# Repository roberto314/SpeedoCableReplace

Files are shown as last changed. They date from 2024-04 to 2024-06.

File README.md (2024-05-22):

# SpeedoCableReplace
An electronic replacement for a Speedometer Cable from an old car.

This is a simple solution for a broken speedometer cable. 
It uses a sensor on the wheels or on the propshaft and converts
it to a PWM for a small BLDC Motor.
I found some on ebay. They look like this:

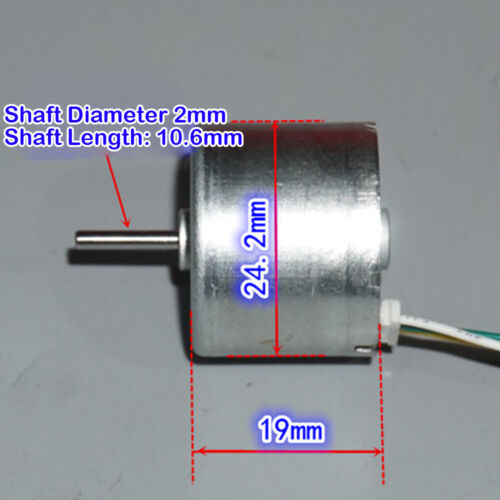
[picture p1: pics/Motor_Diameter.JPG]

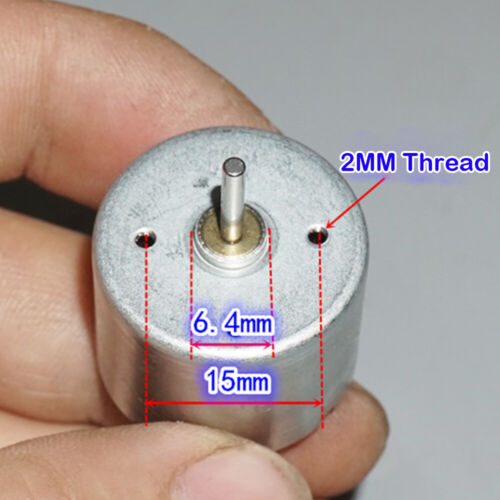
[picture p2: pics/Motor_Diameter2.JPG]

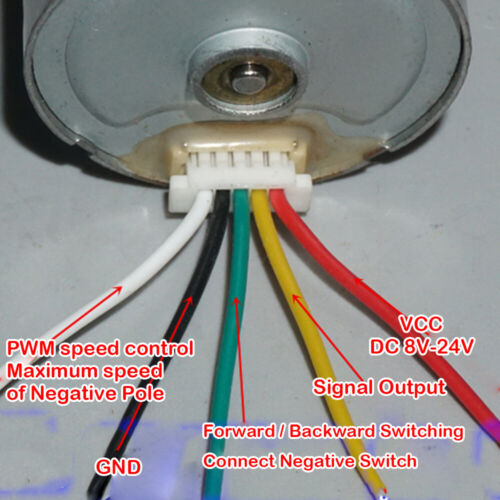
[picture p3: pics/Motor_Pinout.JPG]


This motor should be mounted to the speedometer. The microcontroller is a STM32F103 
maple mini board. The firmware is based on ChibiOS 20 (trunk).

Schematic:

[Schematic](schematics/pdf/Tachoconverter.pdf)

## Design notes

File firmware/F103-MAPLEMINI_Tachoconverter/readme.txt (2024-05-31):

*****************************************************************************
** ChibiOS/RT port for ARM-Cortex-M3 STM32F103 on LeafLabs MapleMini       **
*****************************************************************************

** TARGET **

Tachoconverter

The demo runs on the MapleMini without the original MapleMini bootloader.
Serial Shell @ 38400 Baud, External I2C EPROM, PWM and ICP.

Pinout:
GPIO - mbed - Voltage
PA0  - 11  - 3V3 - free PWM2/1
PA1  - 10  - 3V3 - /HC05ON
PA2  -  9  - 3V3 - TX2 (Console + Debug)
PA3  -  8  - 3V3 - RX2 (Console + Debug)
PA4  -  7  - 3V3 - free
PA5  -  6  - 3V3 - free SPI1 SCK
PA6  -  5  - 3V3 - free SPI1 MISO
PA7  -  4  - 3V3 - free SPI1 MOSI
PA8  - 27  -  5V - VehicleSpeed In PWM1/1
PA9  - 26  -  5V - free PWM1/2
PA10 - 25  -  5V - free PWM1/3
PA11 - 24  -  5V - USD DM 
PA12 - 23  -  5V - USB DP 
PA13 - 22  -  5V - SWDIO
PA14 - 21  -  5V - SWCLK
PA15 - 20  -  5V - free PWM2/1
PB0  -  3  - 3V3 - free
PB1  -  -  -  5V - LED
PB2  -  2  -  5V - free boot
PB3  - 19  -  5V - MotorSpeed In PWM2/2 remap
PB4  - 18  -  5V - CW/CCW PWM3/1
PB5  - 17  - 3V3 - free PWM3/2
PB6  - 16  -  5V - SCL (EPROM)
PB7  - 15  -  5V - SDA (EPROM)
PB8  - but -  5V - MotorPWM Out PWM4/3
PB9  -  -  -  5V - USB_CON
PB10 -  1  -  5V - free PWM2/3
PB11 -  0  -  5V - free PWM2/4
PB12 -  31 -  5V - HC05 State
PB13 -  30 -  5V - free PWM1/1N
PB14 -  29 -  5V - free PWM1/2N
PB15 -  28 -  5V - free PWM1/3N
PC13 -  14 - 3V3 - EPROM WP
PC14 -  13 - 3V3 - HC05 Enable
PC15 -  12 - 3V3 - free

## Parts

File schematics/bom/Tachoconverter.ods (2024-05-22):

Designator | Footprint | Quantity | Designation | Supplier and ref
U2 | TO-220-3_Vertical | 1 | L7805
JP1 | PinHeader_1x03_P2.54mm_Vertical | 1 | SensorVcc
J3 | TerminalBlock_MetzConnect_Type094_RT03505HBLU_1x05_P5.00mm_Horizontal | 1 | Input
A1 | Maple_Mini | 1 | Maple_Mini
J1 | TerminalBlock_MetzConnect_Type094_RT03505HBLU_1x05_P5.00mm_Horizontal | 1 | Motor
D1 | D_SMA | 1 | 1N4007
R5,R6,R1 | R_1206_3216Metric_Pad1.30x1.75mm_HandSolder | 3 | 1k
C3,C1 | CP_EIA-7343-31_Kemet-D | 2 | 100u/25
U1 | DIP-8_W7.62mm_Socket_LongPads | 1 | AT24CS64-SSHM
R2,R4,R3 | R_1206_3216Metric_Pad1.30x1.75mm_HandSolder | 3 | 10k
D2 | SOT-23_Handsoldering | 1 | BAV99
C4,C2 | C_1206_3216Metric_Pad1.33x1.80mm_HandSolder | 2 | 100n
U5 | SOIC-14_3.9x8.7mm_P1.27mm | 1 | 74HC14

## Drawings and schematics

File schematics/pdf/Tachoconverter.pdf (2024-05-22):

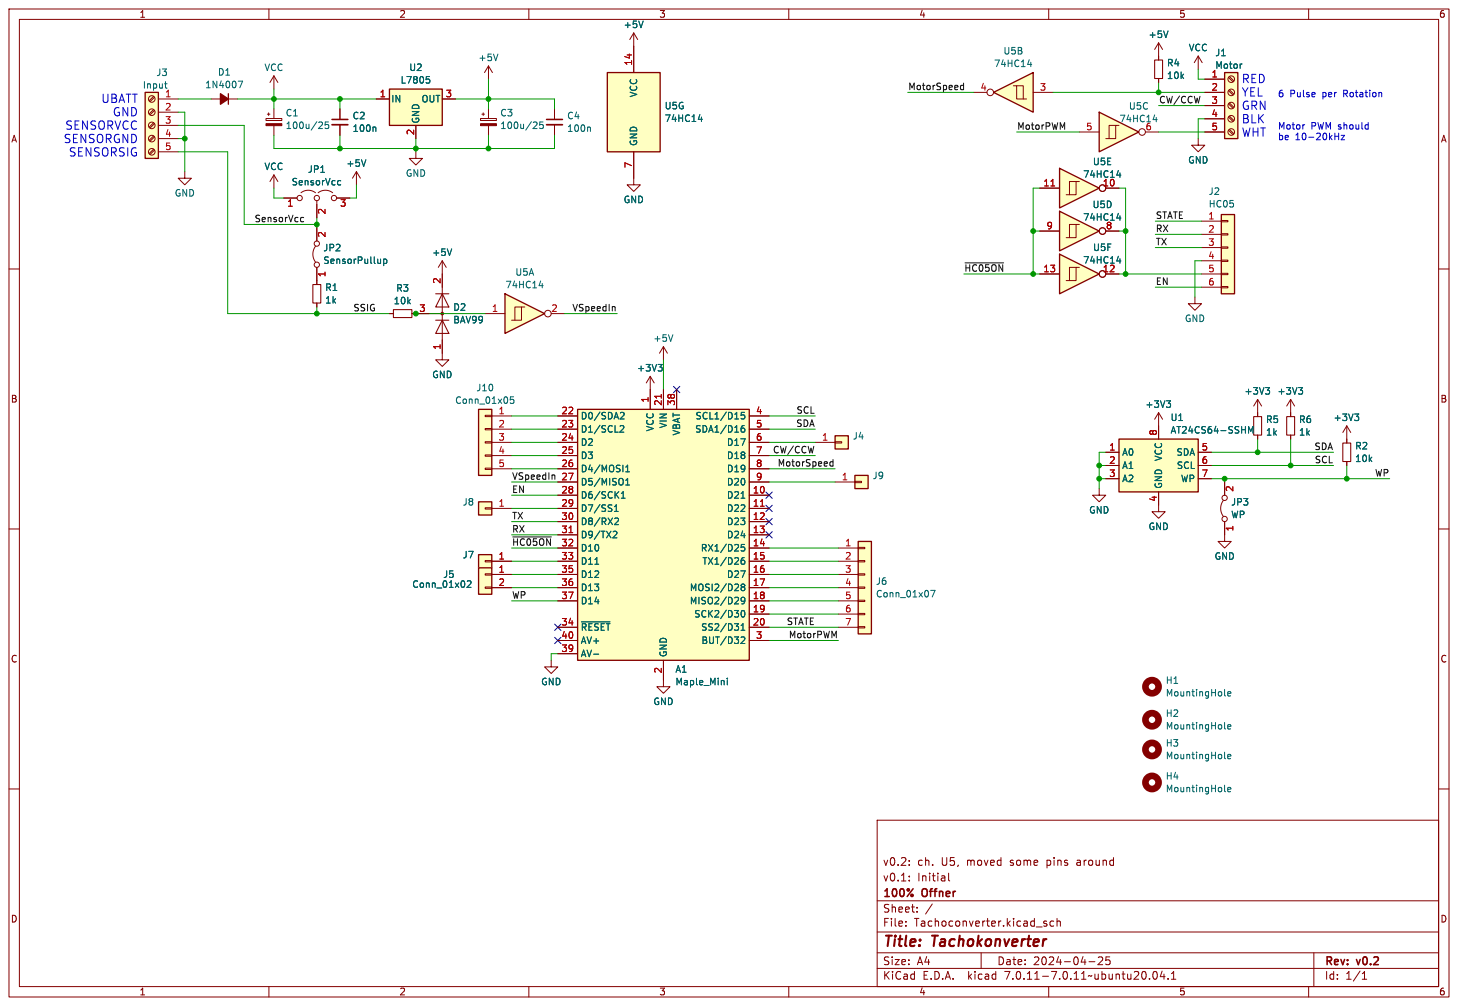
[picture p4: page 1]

6 Pulse per Rotation Motor PWM should

A1Maple_Mini VCC
SDA MotorSpeed STATE MotorPWM

H1 MountingHole H2 MountingHole H3 MountingHole H4 MountingHole GND

2 SS2/D31 20 VIN 21 D0/SDA2 22 D1/SCL2 23 D2 24 D3 25 D4/MOSI1 26 D5/MISO1 27 D6/SCK1 28 D7/SS1 29 BUT/D32 3 D8/RX2 30 D9/TX2 31 D10 32 D11 33 ~{RESET} 34 D12 35 D13 36 D14 37 VBAT 38 AV- 39 SCL1/D15 4 AV+ 40 SDA1/D16 5 D17 6 D18 7 D19 8 D20 9 GND GND

2 SS2/D31 20 VIN 21 D0/SDA2 22 D1/SCL2 23 D2 24 D3 25 D4/MOSI1 26 D5/MISO1 27 D6/SCK1 28 D7/SS1 29 BUT/D32 3 D8/RX2 30 D9/TX2 31 D10 32 D11 33 ~{RESET} 34 D12 35 D13 36 D14 37 VBAT 38 AV- 39 SCL1/D15 4 AV+ 40 SDA1/D16 5 D17 6 D18 7 D19 8 D20 9 A1Maple_Mini GND

4 SDA 5 SCL 6 WP 7 VCC
JP3 WP GND

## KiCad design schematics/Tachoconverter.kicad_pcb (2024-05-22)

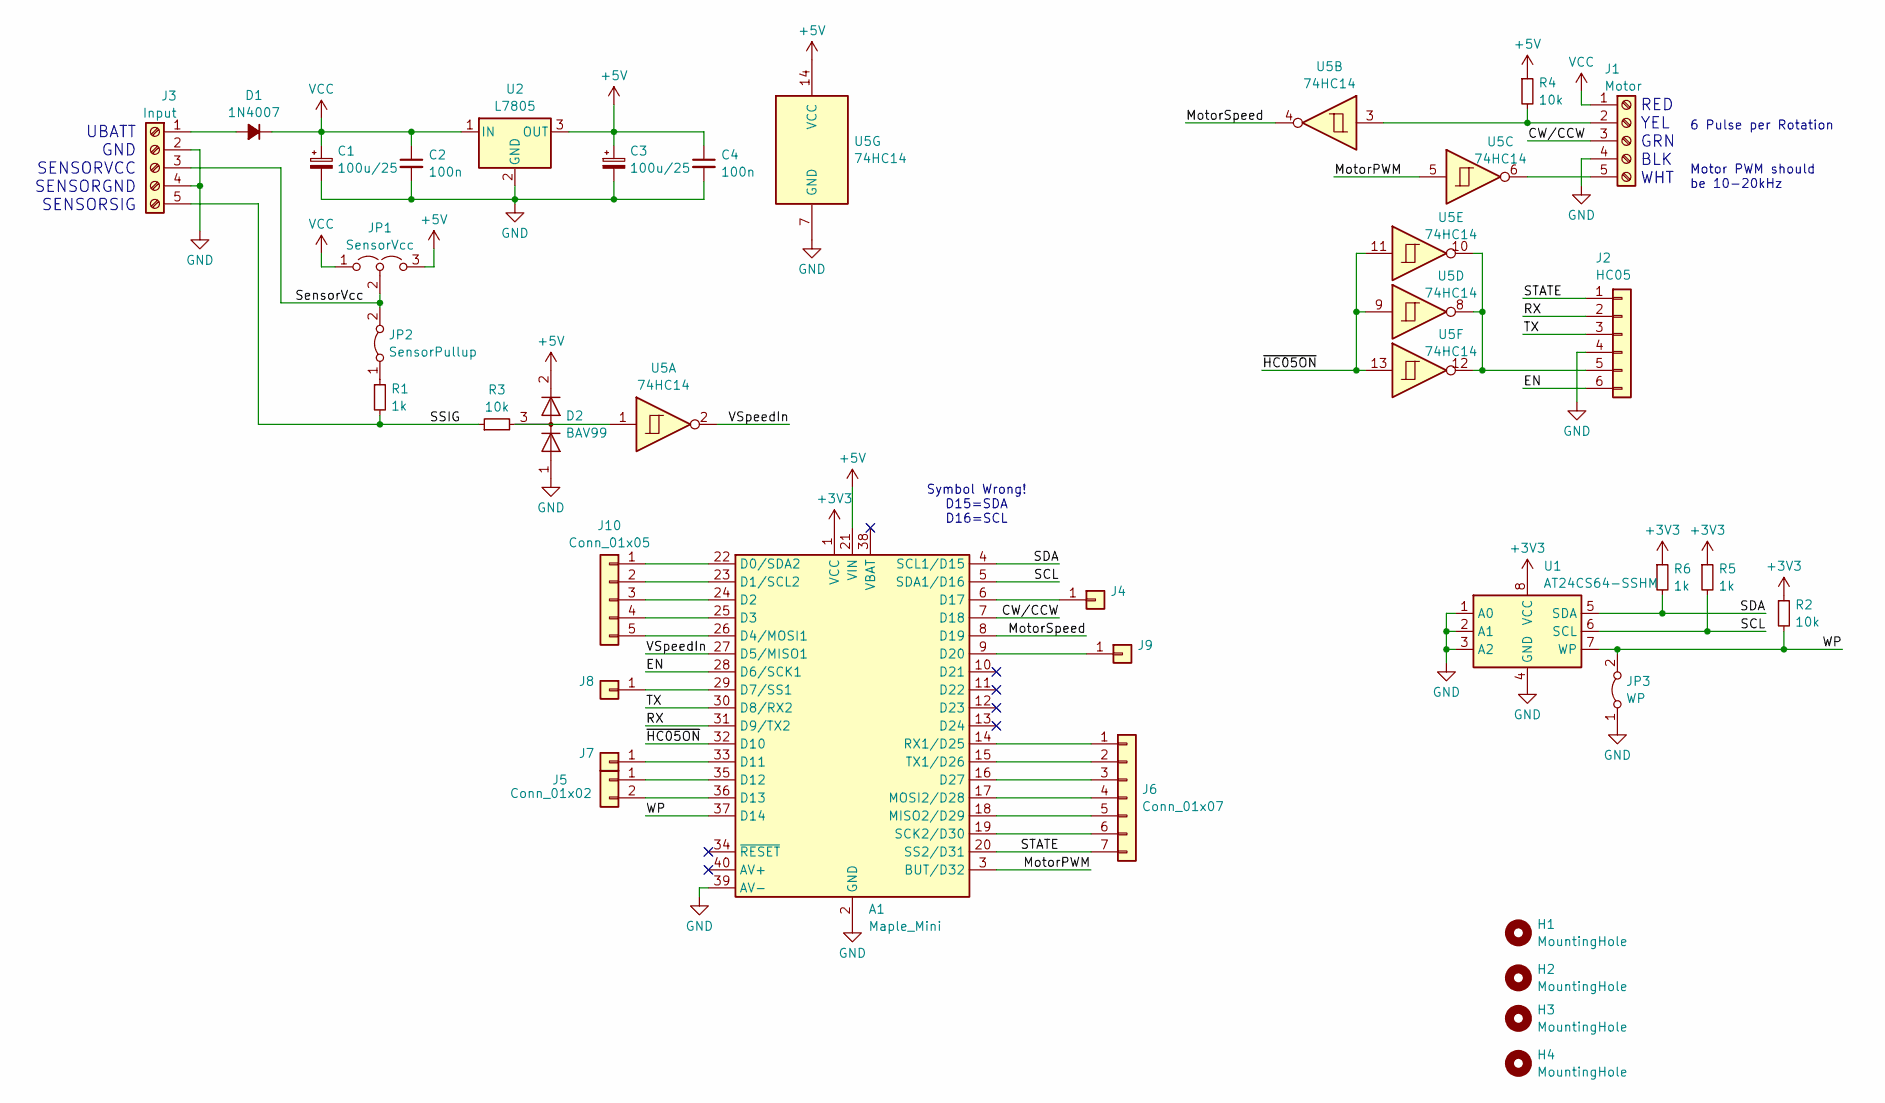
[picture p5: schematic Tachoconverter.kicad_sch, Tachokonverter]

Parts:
A1: Maple_Mini
C1, C3: 100u/25; CP_EIA-7343-31_Kemet-D
C2, C4: 100n; C_1206_3216Metric_Pad1.33x1.80mm_HandSolder
D1: 1N4007; D_SMA
D2: BAV99; SOT-23_Handsoldering
H1, H2, H3, H4: MountingHole; MountingHole_3.2mm_M3
J1: Motor; TerminalBlock_MetzConnect_Type094_RT03505HBLU_1x05_P5.00mm_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
J2: HC05; PinHeader_1x06_P2.54mm_Vertical
J3: Input; TerminalBlock_MetzConnect_Type094_RT03505HBLU_1x05_P5.00mm_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
J4, J7, J8, J9: Conn_01x01; PinHeader_1x01_P2.54mm_Vertical
J5: Conn_01x02; PinHeader_1x02_P2.54mm_Vertical
J6: Conn_01x07; PinHeader_1x07_P2.54mm_Vertical
J10: Conn_01x05; PinHeader_1x05_P2.54mm_Vertical
JP1: SensorVcc; PinHeader_1x03_P2.54mm_Vertical
JP2: SensorPullup; SolderJumper-2_P1.3mm_Bridged_RoundedPad1.0x1.5mm
JP3: WP; SolderJumper-2_P1.3mm_Bridged_RoundedPad1.0x1.5mm
R1, R5, R6: 1k; R_1206_3216Metric_Pad1.30x1.75mm_HandSolder
R2, R3, R4: 10k; R_1206_3216Metric_Pad1.30x1.75mm_HandSolder
U1: AT24CS64-SSHM; DIP-8_W7.62mm_Socket_LongPads
U2: L7805; TO-220-3_Vertical
U5: 74HC14; SOIC-14_3.9x8.7mm_P1.27mm

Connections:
+3V3: A1.1 (VCC), R2.1, R5.1, R6.1, U1.8 (VCC)
+5V: A1.21 (VIN), C3.1, C4.1, D2.2 (A), JP1.3 (B), R4.1, U2.3 (OUT), U5.14 (VCC)
/CW/CCW: A1.7 (D18), J1.3
/EN: A1.28 (D6/SCK1), J2.6
/MotorPWM: A1.3 (BUT/D32), U5.5
/MotorSpeed: A1.8 (D19), U5.4
/RX: A1.31 (D9/TX2), J2.2
/SCL: A1.5 (SDA1/D16), R5.2, U1.6 (SCL)
/SDA: A1.4 (SCL1/D15), R6.2, U1.5 (SDA)
/SSIG: J3.5, R1.2, R3.1
/STATE: A1.20 (SS2/D31), J2.1, J6.7
/SensorVcc: J3.3, JP1.2 (C), JP2.2 (B)
/TX: A1.30 (D8/RX2), J2.3
/VSpeedIn: A1.27 (D5/MISO1), U5.2
/WP: A1.37 (D14), JP3.2 (B), R2.2, U1.7 (WP)
/~HC05ON: A1.32 (D10), U5.9, U5.11, U5.13
GND: A1.2 (GND), A1.39 (AV-), C1.2, C2.2, C3.2, C4.2, D2.1 (K), J1.4, J2.4, J3.2, J3.4, JP3.1 (A), U1.1 (A0), U1.2 (A1), U1.3 (A2), U1.4 (GND), U2.2 (GND), U5.7 (GND)
unnamed: A1.22 (D0/SDA2), J10.1
unnamed: A1.23 (D1/SCL2), J10.2
unnamed: A1.24 (D2), J10.3
unnamed: A1.25 (D3), J10.4
unnamed: A1.26 (D4/MOSI1), J10.5
unnamed: A1.29 (D7/SS1), J8.1
unnamed: A1.33 (D11), J7.1
unnamed: A1.35 (D12), J5.1
unnamed: A1.36 (D13), J5.2
unnamed: A1.6 (D17), J4.1
unnamed: A1.9 (D20), J9.1
unnamed: A1.16 (D27), J6.3
unnamed: A1.18 (MISO2/D29), J6.5
unnamed: A1.17 (MOSI2/D28), J6.4
unnamed: A1.14 (RX1/D25), J6.1
unnamed: A1.19 (SCK2/D30), J6.6
unnamed: A1.15 (TX1/D26), J6.2
unnamed: D1.2 (A), J3.1
unnamed: D2.3 (K), R3.2, U5.1
unnamed: J1.2, R4.2, U5.3
unnamed: J1.5, U5.6
unnamed: J2.5, U5.8, U5.10, U5.12
unnamed: JP2.1 (A), R1.1
VCC: C1.1, C2.1, D1.1 (K), J1.1, JP1.1 (A), U2.1 (IN)

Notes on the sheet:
Symbol Wrong! D15=SDA D16=SCL
RED YEL GRN BLK WHT
6 Pulse per Rotation
Motor PWM should be 10-20kHz
UBATT GND SENSORVCC SENSORGND SENSORSIG

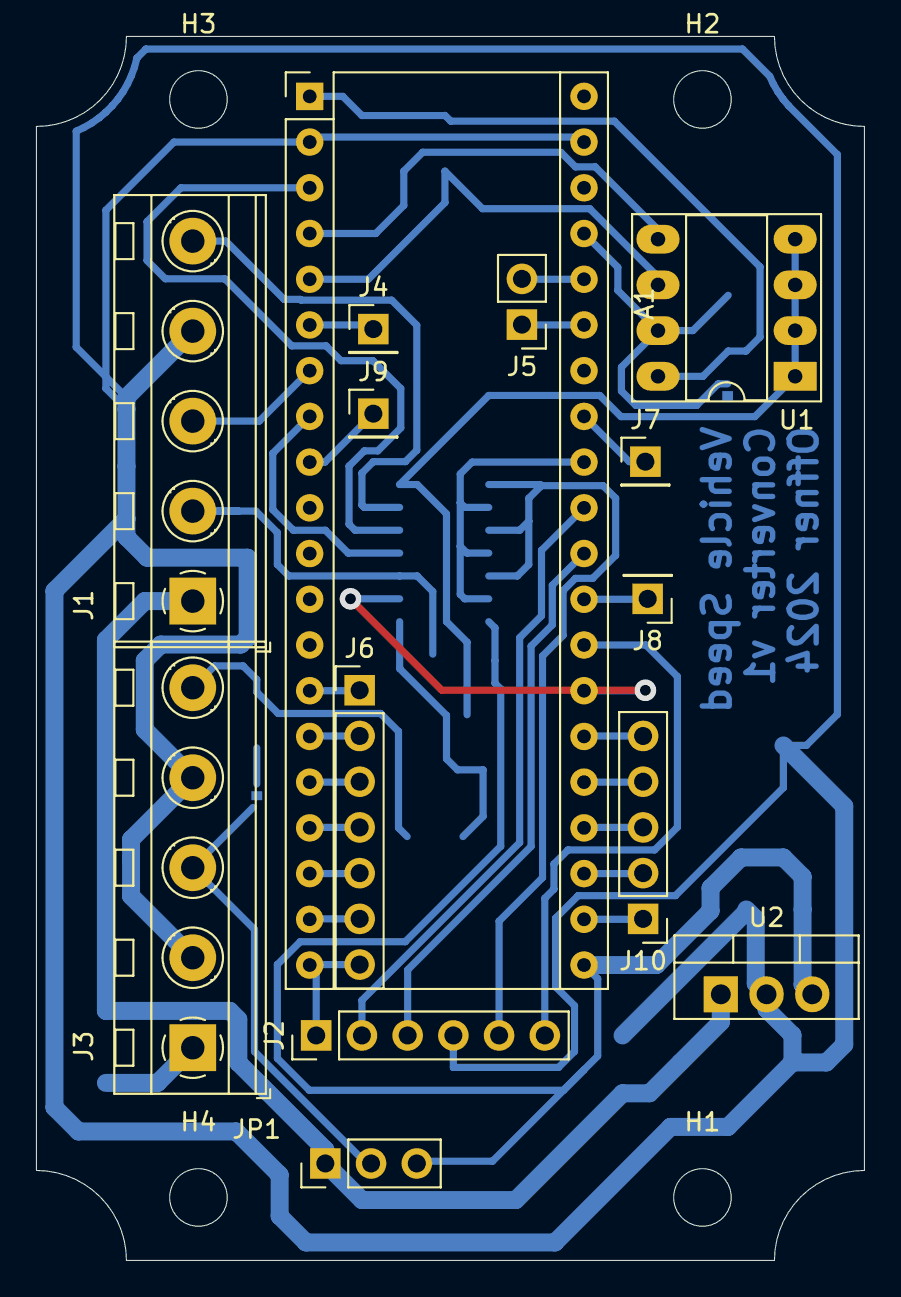
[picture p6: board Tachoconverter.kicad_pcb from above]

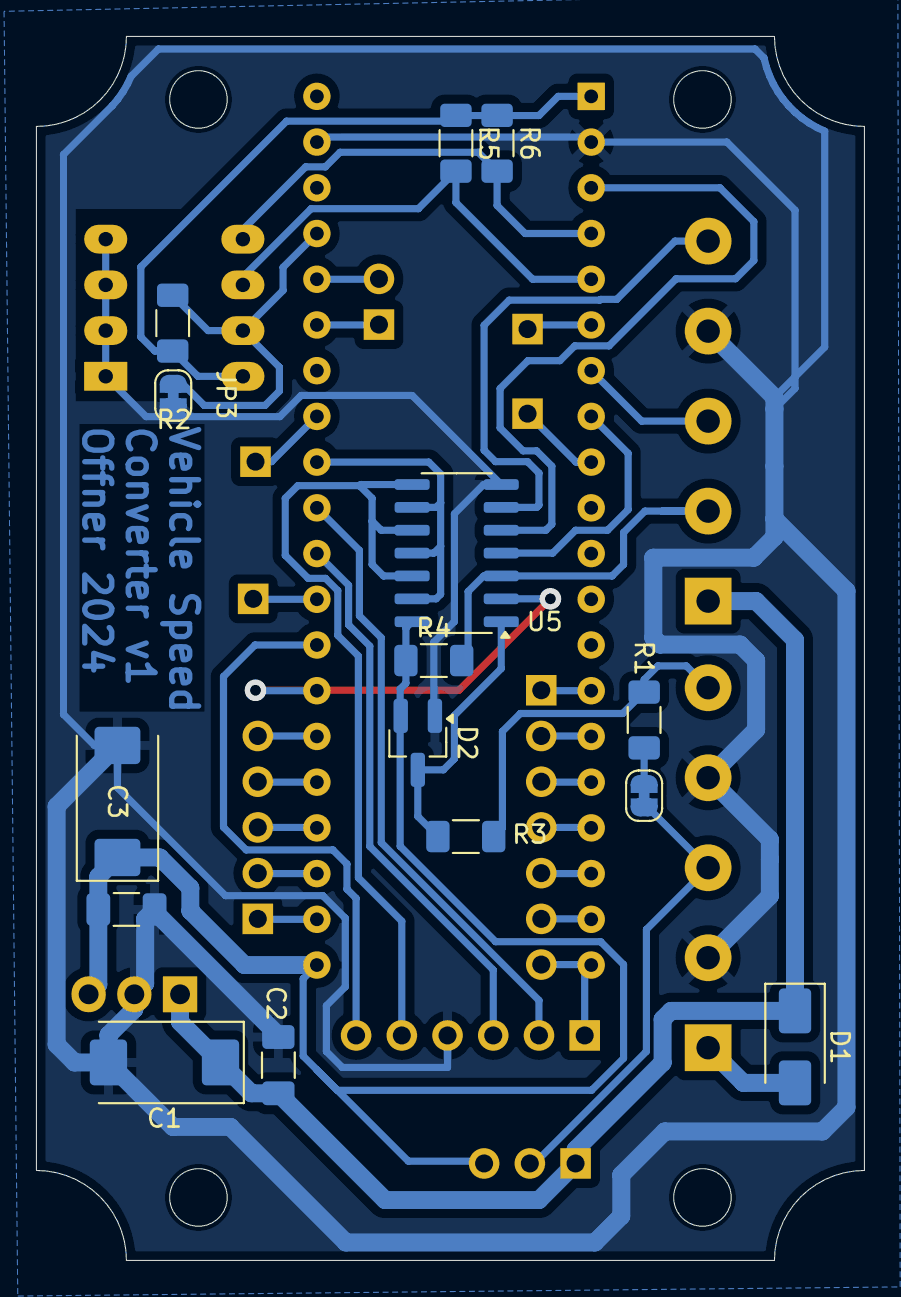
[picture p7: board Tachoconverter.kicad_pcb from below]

Board: 2 copper layers, 46.0 x 68.0 mm, 33 parts (15 on the bottom side), 41 nets.

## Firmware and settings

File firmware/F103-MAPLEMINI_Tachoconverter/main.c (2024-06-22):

/*
    ChibiOS - Copyright (C) 2006..2018 Giovanni Di Sirio

    Licensed under the Apache License, Version 2.0 (the "License");
    you may not use this file except in compliance with the License.
    You may obtain a copy of the License at

        http://www.apache.org/licenses/LICENSE-2.0

    Unless required by applicable law or agreed to in writing, software
    distributed under the License is distributed on an "AS IS" BASIS,
    WITHOUT WARRANTIES OR CONDITIONS OF ANY KIND, either express or implied.
    See the License for the specific language governing permissions and
    limitations under the License.
*/
#include "string.h"
#include "stdint.h"
#include "stdlib.h" //to get rid of compiler warnings
#include "ch.h"
#include "hal.h"
#include "chprintf.h" //to get rid of compiler warnings
#include "shell.h"
#include "comm.h"
#include "table.h"
#include "i2c_local.h"
#include "eeprom.h"
#include "hc05.h"
//################################################################################################
//                                  Static Variables
#define ICPCLKFREQ 36000000
uint16_t real_freq, f_enable = 0;
uint32_t pwm_in;
float speed_in;
uint16_t cnt;
//icucnt_t last_width;
uint32_t last_period;
configunion_t cudata = {
        .configstruct.ver = CONFIG_VERSION,
        .configstruct.chksm = CHECKSUM,
        .configstruct.table0.t_length = 23,
        .configstruct.table0.in[0] =     0,   10,   20,   30,   40,   50,   60,   70,   80,   90,  100,  110,  120,  130,  140,  150,  160,  170, 180,  190,  200,  210, 220,
        .configstruct.table0.out[0] = 1000, 1660, 1880, 2270, 2660, 3100, 3380, 3800, 4100, 4600, 5010, 5370, 5770, 6210, 6600, 7040, 7340, 7710, 8150, 8540, 8870, 9370, 9770
// PERIOD

};
/*
configunion_t cudata = {
        .configstruct.table0.t_length = 23,
        .configstruct.table0.in[0] = 0, 10, 20, 30, 40, 50, 60, 70, 80, 90, 100, 110, 120, 130, 140, 150, 160, 170, 180, 190, 200, 210, 220,
        .configstruct.table0.out[0] = 48000, 24100, 12000, 8180, 6040, 4810, 3990, 3430, 2990, 2650, 2380, 2140, 1960, 1810, 1677, 1565, 1470, 1385, 1308, 1240, 1175, 1122, 1071,
        .configstruct.corr = 1050
};
*/
//################################################################################################
//                                  Function declarations
void PWM_Off(void);
void ch_fSpeed(uint16_t speed);
//################################################################################################

static PWMConfig pwmcfg = {
  ICPCLKFREQ,                              // 18MHz initial clock frequency.
  1800,                                    // Initial PWM period 100uS (10kHz).
  NULL,
  {
   {PWM_OUTPUT_DISABLED, NULL},
   {PWM_OUTPUT_DISABLED, NULL},
   {PWM_OUTPUT_ACTIVE_HIGH, NULL},
   {PWM_OUTPUT_DISABLED, NULL}
  },
  0,
  0,
#if STM32_PWM_USE_ADVANCED
  0
#endif
};
/* This is the config and callbacks for the
 * ICP Input for the BLDC Motor feedback
 * on TIM2/2 (remaped to PB3)
 *
 */
static void icuperiodcb(ICUDriver *icup) {
    //float temp = 2*ICPCLKFREQ/4.42;
    //static uint16_t cnt;
    //last_period += (uint32_t)icuGetPeriodX(icup);
  last_period = (float)icuGetPeriodX(icup);
    cnt++;
    /*if (cnt >= 2){
        cnt = 0;
        real_freq = (uint16_t)(temp/last_period);
        last_period = 0;
    }*/
}

static void icuoverflowcb(ICUDriver *icup) {
    (void) icup;
    //real_freq = 0;
    speed_in = 0;
    cnt = 0;
}
static ICUConfig icucfg = {
  ICU_INPUT_ACTIVE_LOW,
  100000,                              // 100kHz initial ICU clock frequency.
  NULL,
  icuperiodcb,
  icuoverflowcb,
  ICU_CHANNEL_2,
  0,
  0xFFFFFFFFU
};

/*===========================================================================*/
/* Command line related.                                                     */
/*===========================================================================*/
#define SHELL_WA_SIZE   THD_WORKING_AREA_SIZE(2048)
char history_buffer[8*64];
static const ShellCommand commands[] = {
  {"vstat", cmd_status},
  {"mod", cmd_modify},
  {"stl", cmd_stl},
  {"smm", cmd_smm},
  {"scf", cmd_scf},
  {"cpwm", cmd_ch_pwm},
  {"cspd", cmd_ch_speed},
  {"cfspd", cmd_ch_fspeed},
  {"cspdcf", cmd_ch_speed_cf},
  {"tspd", cmd_tune_speed},
  {"dumpvar", cmd_dumpvar},
  {"dumpee", cmd_dumpee},
  {"writee", cmd_writee},
  {"fillee", cmd_fillee},
  {"confrd", cmd_confrd},
  {"confwrt", cmd_confwrt},
  //{"ctimf", cmd_ch_tim_freq},
  {"per", cmd_per},
  {"dis", cmd_dis},
  {"dir", cmd_dir},
  {"cinpf", cmd_ch_inp_f},
  {NULL, NULL}
 };

static const ShellConfig shell_cfg1 = {
  (BaseSequentialStream *)&SD2,
  commands,
  history_buffer,
  sizeof(history_buffer)
};

/*===========================================================================*/
/* Generic code.                                                             */
/*===========================================================================*/
//uint32_t get_tim_freq(TIM_TypeDef * TIMP){
//      uint32_t freq, clock;
//      uint16_t psc = TIMP->PSC;
//      clock = STM32_TIMCLK1;
//      freq = clock / (psc+1);
//      return freq;
//}
//void set_tim_freq(TIM_TypeDef * TIMP, uint32_t freq){
//      uint32_t clock;
//      uint16_t psc;
//      clock = STM32_TIMCLK1;
//      psc = (clock / (freq )) - 1;
//      TIMP->PSC = psc;
//}
void update_pwm(void){
    float temp;
    temp = speed_in / cnt; //averaging
    speed_in = 0;
    cnt = 0;
    //last_period = (uint16_t) temp;
    temp *= cudata.configstruct.fs_corr;  //conversion from frequency to real speed
    temp = 2*ICPCLKFREQ / temp;
    real_freq = (uint16_t)temp;
    //ch_fSpeed((uint16_t)temp);
}
/*
 * Blinker thread.
 */
static THD_WORKING_AREA(waThread1, 128);
static THD_FUNCTION(Thread1, arg) {

  (void)arg;
  static uint16_t cnt = 0;
  chRegSetThreadName("blinker");
  while (true) {
      cnt++;
      if (cnt >= 5){
          palTogglePad(GPIOB, GPIOB_LED);
          cnt = 0;
      }

      //palSetPad(GPIOC, GPIOC_LED);
      //chThdSleepMilliseconds(500);
      //palClearPad(GPIOC, GPIOC_LED);
      if (f_enable > 0){
          update_pwm();
      }

      chThdSleepMilliseconds(100);
  }
}
void PWM_Off(void){
    pwmDisableChannel(&PWMD4, 3);
}
void ch_PWM_Freq(uint32_t freq){
    pwm_in = freq;
    pwmChangePeriod(&PWMD4, freq);
    pwmEnableChannel(&PWMD4, 2, PWM_PERCENTAGE_TO_WIDTH(&PWMD4, 5000));
    //pwmEnableChannelNotification(&PWMD4, 2);
}
void ch_Speed(uint16_t speed){
    //table lookup here!
  ch_PWM_Freq(read_table_u16(&(cudata.configstruct.table0), speed));
}
void ch_fSpeed(uint16_t speed){ // fspeed is Fake speed. It uses a correction factor (corr)
                                // to show (usually) more speed as in reality.
    uint32_t fspeed;
    fspeed = (uint32_t)(speed)*cudata.configstruct.corr;
    ch_Speed((uint16_t)(fspeed / 1000));
}
/*
 * Application entry point.
 */
int main(void) {
  thread_t *shelltp = NULL;
  /*
   * System initializations.
   * - HAL initialization, this also initializes the configured device drivers
   *   and performs the board-specific initializations.
   * - Kernel initialization, the main() function becomes a thread and the
   *   RTOS is active.
   */
  halInit();
  chSysInit();
  AFIO->MAPR |= AFIO_MAPR_SWJ_CFG_JTAGDISABLE; //PB3, PB4, PA15 working, PA13, PA14 NOT
  //AFIO->MAPR |= AFIO_MAPR_SWJ_CFG_DISABLE;     //PB3, PB4, PA15, PA13, PA14 working
  AFIO->MAPR |= AFIO_MAPR_TIM2_REMAP_0; // Partial Remap PWM2/2 to PB3

  pwmStart(&PWMD4, &pwmcfg);
  pwmEnablePeriodicNotification(&PWMD4);
  // TIM1 Outputs
  palSetPadMode(GPIOB, 8, PAL_MODE_STM32_ALTERNATE_PUSHPULL); //TIM4-CH3, Motor PWM out

  /*
   * Starts the PWM channel 1 using 30% duty cycle.
   */
//  pwmEnableChannel(&PWMD4, 2, PWM_PERCENTAGE_TO_WIDTH(&PWMD4, 3000));
//  pwmEnableChannelNotification(&PWMD4, 2);
  //ch_PWM_Freq(600000);

  icuStart(&ICUD2, &icucfg);
  icuStartCapture(&ICUD2);
  icuEnableNotifications(&ICUD2);
  palSetPadMode(GPIOB, 3, PAL_MODE_INPUT_PULLUP); //TIM2-CH2 Motor Speed feedback
  /*
   * Activates the serial driver 2 using the driver default configuration.
   * PA2(TX) and PA3(RX) are routed to USART2.
   */
  sdStart(&SD2, NULL);
  palSetPadMode(GPIOA, 2, PAL_MODE_STM32_ALTERNATE_PUSHPULL); //UART TX
  palSetPadMode(GPIOB, 4, PAL_MODE_OUTPUT_PUSHPULL); //CW/CCW
  palClearPad(GPIOB, 4); // set to counterclockwise
  palClearPad(GPIOC, 13); // Set EPROM to Write Protect Off
  palSetPadMode(GPIOC, 13, PAL_MODE_OUTPUT_PUSHPULL); // EPROM WP

  chprintf((BaseSequentialStream *)&SD2, "ChibiOS Bluepill F103 Shell v0.1\r\n");
  /*
   * Shell manager initialization.
   */
  shellInit();
  I2CInitLocal(); //Starts I2C Driver
  configInit();    //checks config version and checksum and, if OK, copies it to RAM
  hc05_init();
  /*
   * Creates the example thread.
   */
  chThdCreateStatic(waThread1, sizeof(waThread1), NORMALPRIO+1, Thread1, NULL);

  /*
   * Normal main() thread activity, in this demo it does nothing except
   * sleeping in a loop and check the button state, when the button is
   * pressed the test procedure is launched.
   */
  while (true) {
    if (!shelltp)
      shelltp = chThdCreateFromHeap(NULL, SHELL_WA_SIZE,
                                    "shell", NORMALPRIO + 1,
                                    shellThread, (void *)&shell_cfg1);
    else if (chThdTerminatedX(shelltp)) {
      chThdRelease(shelltp);    /* Recovers memory of the previous shell.   */
      shelltp = NULL;           /* Triggers spawning of a new shell.        */
    }
    chThdSleepMilliseconds(500);
  }
}

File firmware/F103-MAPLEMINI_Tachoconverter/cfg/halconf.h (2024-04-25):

/*
    ChibiOS - Copyright (C) 2006..2018 Giovanni Di Sirio

    Licensed under the Apache License, Version 2.0 (the "License");
    you may not use this file except in compliance with the License.
    You may obtain a copy of the License at

        http://www.apache.org/licenses/LICENSE-2.0

    Unless required by applicable law or agreed to in writing, software
    distributed under the License is distributed on an "AS IS" BASIS,
    WITHOUT WARRANTIES OR CONDITIONS OF ANY KIND, either express or implied.
    See the License for the specific language governing permissions and
    limitations under the License.
*/

/**
 * @file    templates/halconf.h
 * @brief   HAL configuration header.
 * @details HAL configuration file, this file allows to enable or disable the
 *          various device drivers from your application. You may also use
 *          this file in order to override the device drivers default settings.
 *
 * @addtogroup HAL_CONF
 * @{
 */

#ifndef HALCONF_H
#define HALCONF_H

#define _CHIBIOS_HAL_CONF_
#define _CHIBIOS_HAL_CONF_VER_7_1_

#include "mcuconf.h"

/**
 * @brief   Enables the PAL subsystem.
 */
#if !defined(HAL_USE_PAL) || defined(__DOXYGEN__)
#define HAL_USE_PAL                         TRUE
#endif

/**
 * @brief   Enables the ADC subsystem.
 */
#if !defined(HAL_USE_ADC) || defined(__DOXYGEN__)
#define HAL_USE_ADC                         FALSE
#endif

/**
 * @brief   Enables the CAN subsystem.
 */
#if !defined(HAL_USE_CAN) || defined(__DOXYGEN__)
#define HAL_USE_CAN                         FALSE
#endif

/**
 * @brief   Enables the cryptographic subsystem.
 */
#if !defined(HAL_USE_CRY) || defined(__DOXYGEN__)
#define HAL_USE_CRY                         FALSE
#endif

/**
 * @brief   Enables the DAC subsystem.
 */
#if !defined(HAL_USE_DAC) || defined(__DOXYGEN__)
#define HAL_USE_DAC                         FALSE
#endif

/**
 * @brief   Enables the EFlash subsystem.
 */
#if !defined(HAL_USE_EFL) || defined(__DOXYGEN__)
#define HAL_USE_EFL                         FALSE
#endif

/**
 * @brief   Enables the GPT subsystem.
 */
#if !defined(HAL_USE_GPT) || defined(__DOXYGEN__)
#define HAL_USE_GPT                         FALSE
#endif

/**
 * @brief   Enables the I2C subsystem.
 */
#if !defined(HAL_USE_I2C) || defined(__DOXYGEN__)
#define HAL_USE_I2C                         TRUE//FALSE
#endif

/**
 * @brief   Enables the I2S subsystem.
 */
#if !defined(HAL_USE_I2S) || defined(__DOXYGEN__)
#define HAL_USE_I2S                         FALSE
#endif

/**
 * @brief   Enables the ICU subsystem.
 */
#if !defined(HAL_USE_ICU) || defined(__DOXYGEN__)
#define HAL_USE_ICU                         TRUE//FALSE
#endif

/**
 * @brief   Enables the MAC subsystem.
 */
#if !defined(HAL_USE_MAC) || defined(__DOXYGEN__)
#define HAL_USE_MAC                         FALSE
#endif

/**
 * @brief   Enables the MMC_SPI subsystem.
 */
#if !defined(HAL_USE_MMC_SPI) || defined(__DOXYGEN__)
#define HAL_USE_MMC_SPI                     FALSE
#endif

/**
 * @brief   Enables the PWM subsystem.
 */
#if !defined(HAL_USE_PWM) || defined(__DOXYGEN__)
#define HAL_USE_PWM                         TRUE//FALSE
#endif

/**
 * @brief   Enables the RTC subsystem.
 */
#if !defined(HAL_USE_RTC) || defined(__DOXYGEN__)
#define HAL_USE_RTC                         FALSE
#endif

/**
 * @brief   Enables the SDC subsystem.
 */
#if !defined(HAL_USE_SDC) || defined(__DOXYGEN__)
#define HAL_USE_SDC                         FALSE
#endif

/**
 * @brief   Enables the SERIAL subsystem.
 */
#if !defined(HAL_USE_SERIAL) || defined(__DOXYGEN__)
#define HAL_USE_SERIAL                      TRUE//FALSE
#endif

/**
 * @brief   Enables the SERIAL over USB subsystem.
 */
#if !defined(HAL_USE_SERIAL_USB) || defined(__DOXYGEN__)
#define HAL_USE_SERIAL_USB                  FALSE//TRUE
#endif

/**
 * @brief   Enables the SIO subsystem.
 */
#if !defined(HAL_USE_SIO) || defined(__DOXYGEN__)
#define HAL_USE_SIO                         FALSE
#endif

/**
 * @brief   Enables the SPI subsystem.
 */
#if !defined(HAL_USE_SPI) || defined(__DOXYGEN__)
#define HAL_USE_SPI                         FALSE
#endif

/**
 * @brief   Enables the TRNG subsystem.
 */
#if !defined(HAL_USE_TRNG) || defined(__DOXYGEN__)
#define HAL_USE_TRNG                        FALSE
#endif

/**
 * @brief   Enables the UART subsystem.
 */
#if !defined(HAL_USE_UART) || defined(__DOXYGEN__)
#define HAL_USE_UART                        FALSE
#endif

/**
 * @brief   Enables the USB subsystem.
 */
#if !defined(HAL_USE_USB) || defined(__DOXYGEN__)
#define HAL_USE_USB                         FALSE//TRUE
#endif

/**
 * @brief   Enables the WDG subsystem.
 */
#if !defined(HAL_USE_WDG) || defined(__DOXYGEN__)
#define HAL_USE_WDG                         FALSE
#endif

/**
 * @brief   Enables the WSPI subsystem.
 */
#if !defined(HAL_USE_WSPI) || defined(__DOXYGEN__)
#define HAL_USE_WSPI                        FALSE
#endif

/*===========================================================================*/
/* PAL driver related settings.                                              */
/*===========================================================================*/

/**
 * @brief   Enables synchronous APIs.
 * @note    Disabling this option saves both code and data space.
 */
#if !defined(PAL_USE_CALLBACKS) || defined(__DOXYGEN__)
#define PAL_USE_CALLBACKS                   FALSE
#endif

/**
 * @brief   Enables synchronous APIs.
 * @note    Disabling this option saves both code and data space.
 */
#if !defined(PAL_USE_WAIT) || defined(__DOXYGEN__)
#define PAL_USE_WAIT                        FALSE
#endif

/*===========================================================================*/
/* ADC driver related settings.                                              */
/*===========================================================================*/

/**
 * @brief   Enables synchronous APIs.
 * @note    Disabling this option saves both code and data space.
 */
#if !defined(ADC_USE_WAIT) || defined(__DOXYGEN__)
#define ADC_USE_WAIT                        TRUE
#endif

/**
 * @brief   Enables the @p adcAcquireBus() and @p adcReleaseBus() APIs.
 * @note    Disabling this option saves both code and data space.
 */
#if !defined(ADC_USE_MUTUAL_EXCLUSION) || defined(__DOXYGEN__)
#define ADC_USE_MUTUAL_EXCLUSION            TRUE
#endif

/*===========================================================================*/
/* CAN driver related settings.                                              */
/*===========================================================================*/

/**
 * @brief   Sleep mode related APIs inclusion switch.
 */
#if !defined(CAN_USE_SLEEP_MODE) || defined(__DOXYGEN__)
#define CAN_USE_SLEEP_MODE                  TRUE
#endif

/**
 * @brief   Enforces the driver to use direct callbacks rather than OSAL events.
 */
#if !defined(CAN_ENFORCE_USE_CALLBACKS) || defined(__DOXYGEN__)
#define CAN_ENFORCE_USE_CALLBACKS           FALSE
#endif
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

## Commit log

2024-04-25 board changed
    [Tachoconverter-B_Cu.gbr, Tachoconverter-B_Mask.gbr, Tachoconverter-B_Paste.gbr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]
2024-05-22 schematic update
    [Tachoconverter-B_Cu.gbr, Tachoconverter-B_Mask.gbr, Tachoconverter-B_Paste.gbr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]
